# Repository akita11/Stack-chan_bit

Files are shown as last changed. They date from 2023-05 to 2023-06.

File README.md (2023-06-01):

# Stack-chan_bit

[ｽﾀｯｸﾁｬﾝ](https://protopedia.net/prototype/2345Stack-chan)に[micro:bit](https://www.switch-science.com/products/7952)を差し込んで制御するボードです。micro:bitのプログラミングでｽﾀｯｸﾁｬﾝを動かすことができます。

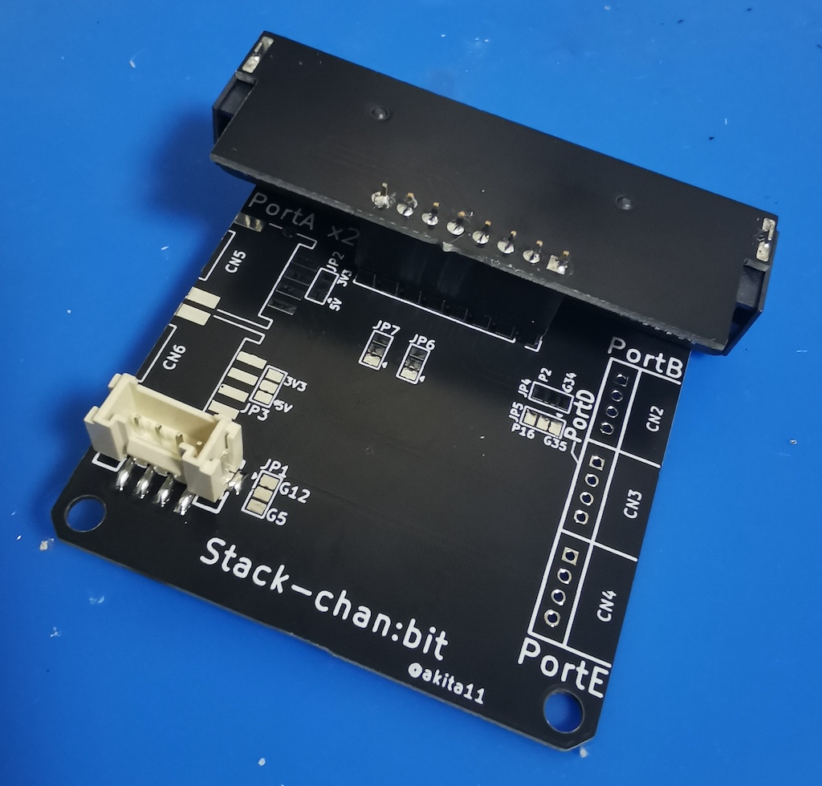
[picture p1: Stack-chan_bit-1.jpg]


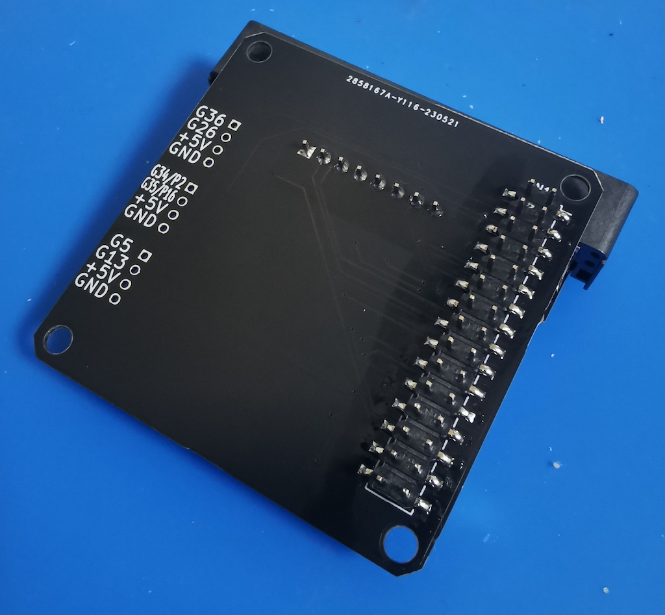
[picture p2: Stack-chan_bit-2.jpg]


## 使用例

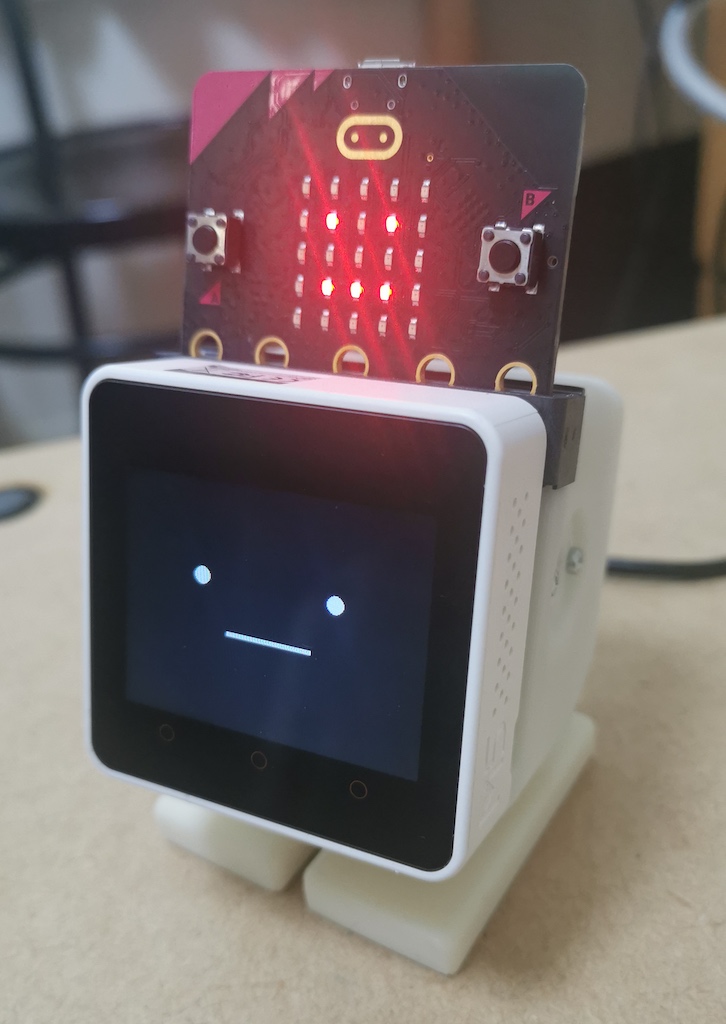
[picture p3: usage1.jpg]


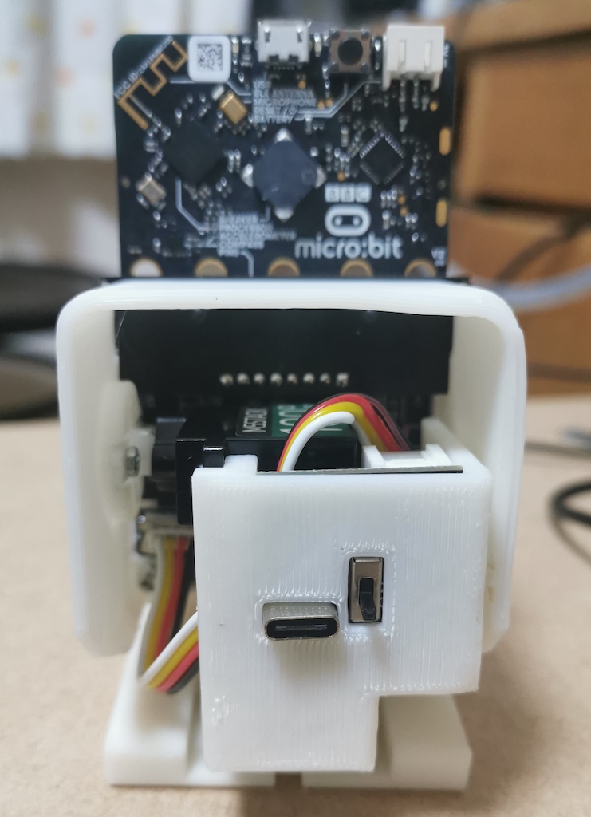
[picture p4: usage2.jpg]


micro:bit側のプログラム（m-asaoka-fap氏作成の[カスタムブロック](https://github.com/m-asaoka-fap/stackchanbit_2)あり）から、ｽﾀｯｸﾁｬﾝを制御できます。→[使用例](https://twitter.com/akita11/status/1656496746321842176)

## 作り方

### 用意するもの

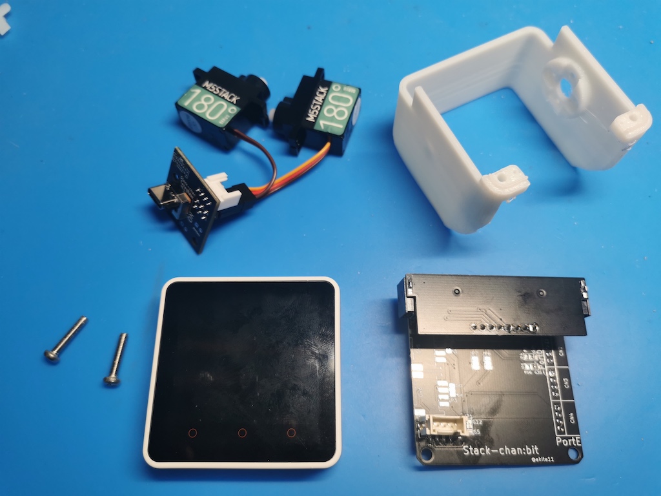
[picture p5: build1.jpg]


- M5Stack (BasicまたはCore2がオススメ)
- [Stack-chan_Takao_Base](https://github.com/akita11/Stack-chan_Takao_Base)とそれで用いるもの（サーボモータ2個、Groveケーブル、ネジ等、筐体(shell部以外)）※顔部分のM5Stack本体との固定には、BasicではM3x15mm、Core2ではM3x20mmのネジを2本使います
- shell部の筐体(Stack-chan_bit_shell.stlを3Dプリントしたもの): [タカオ版筐体](https://github.com/meganetaaan/stack-chan/tree/dev/v1.0/case/contributed/mongonta_case_for_SG90_and_M5GoBottomBoard/case_for_SG90andM5GoBottomBoard)内の”shell_SG90_basicgraybottom_v1.0.stl"を元に改変

### 組み立て

M5Stackに専用プログラム（FW_PIO/以下。PlatformIO用）を書き込みます。

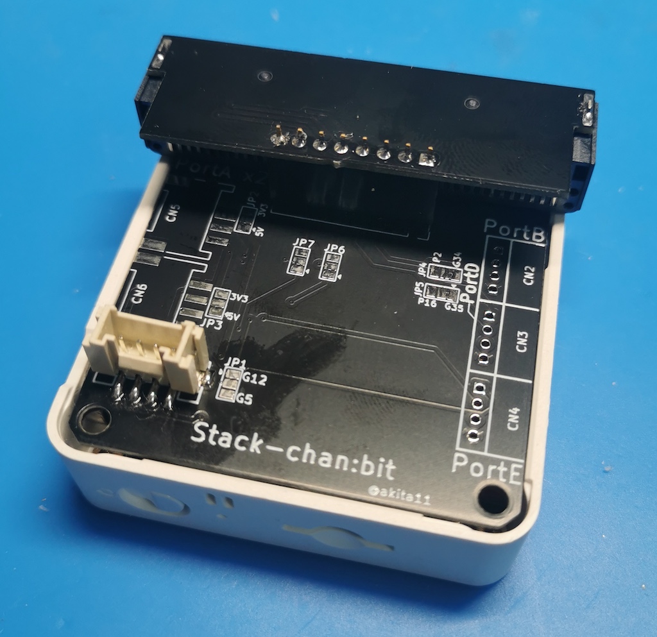
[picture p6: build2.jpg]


M5Stackの底板を外し、Stack-chan_bitをさしこみます。

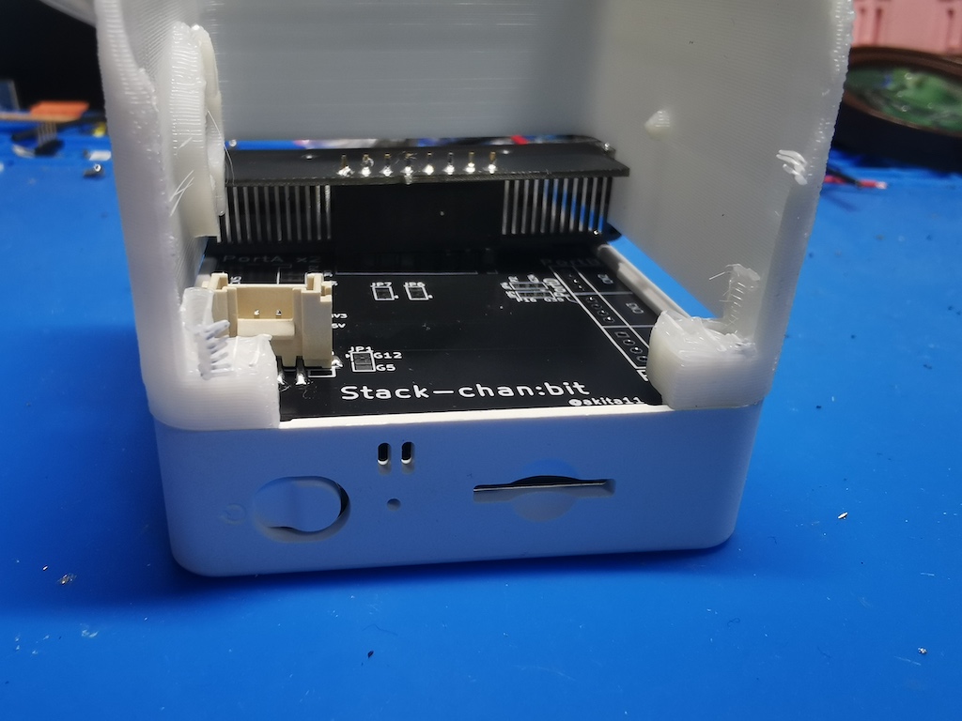
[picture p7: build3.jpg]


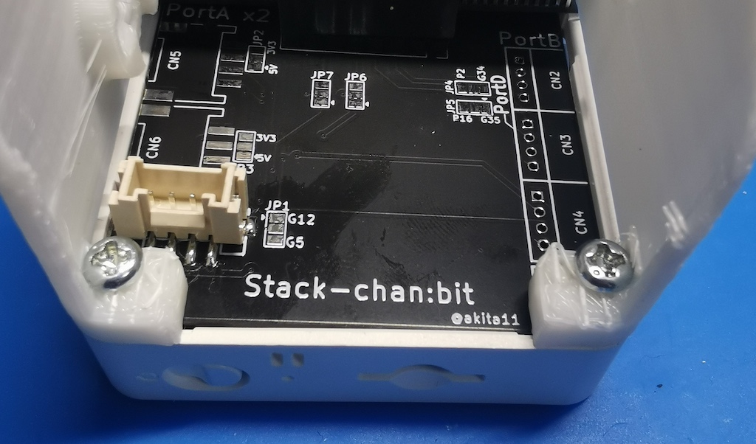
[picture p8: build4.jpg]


2本のM3ネジで固定します

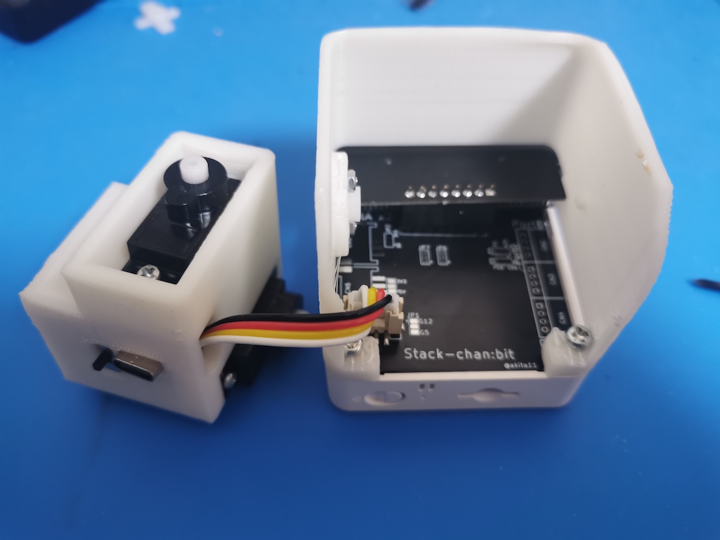
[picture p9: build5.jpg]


[Stack-chan_Takao_Base](https://github.com/akita11/Stack-chan_Takao_Base)を使って
Bracket部（サーボ2個が固定される部分）を組み立てつつ、Stack-chan:bit基板と、Groveケーブルで接続します。

残りの部分は、Stack-chan_Takao_BaseからのGroveケーブルは、M5Stack本体ではなく、Stack-chan_bitのGroveコネクタに接続する

残りの部分は、[タカオさんの手順](https://raspberrypi.mongonta.com/how-to-build-easy-stackchan-m5gobottom/)を参考に組み立てます。

## プログラミング

micro:bitとｽﾀｯｸﾁｬﾝ(M5Stack)の間はUART通信(115200bps・N81、コマンド区切りはLF/0x0a/'\n'）で以下のような制御コマンドを送って制御します。[micro:bit側のカスタムブロック](https://github.com/m-asaoka-fap/stackchanbit_2)もあり、MakeCoreで組み込んで使用できます。

- 動作の制御
  - Xnn : パン動作（横方向）nn=角度、範囲＝-90〜90（正面=0）
  - Ynn : チルト動作（縦方向）nn=角度、範囲=0〜30（正面=0から上向きへ）
- 顔の制御
  - Txxxx : 吹き出しに”xxxx”と表示し、それにあわせて口が動く
  - En : 表情を設定。n=0〜5 (0=Angry, 1=Sleepy, 2=Happy, 3=Sat, 4=Doubt, 5=Neutral)

## （おまけ）拡張用Grove端子

M5Stackやmicro:bitの一部の端子をGrove端子に引き出せるようにGroveコネクタ実装部が用意してあります。詳細は回路図を参照してください。ただし使用する場合はGroveコネクタ部分にあわせて筐体(shell)の修正が必要になります。

## Author

Junichi Akita (@akita11, akita@ifdl.jp)

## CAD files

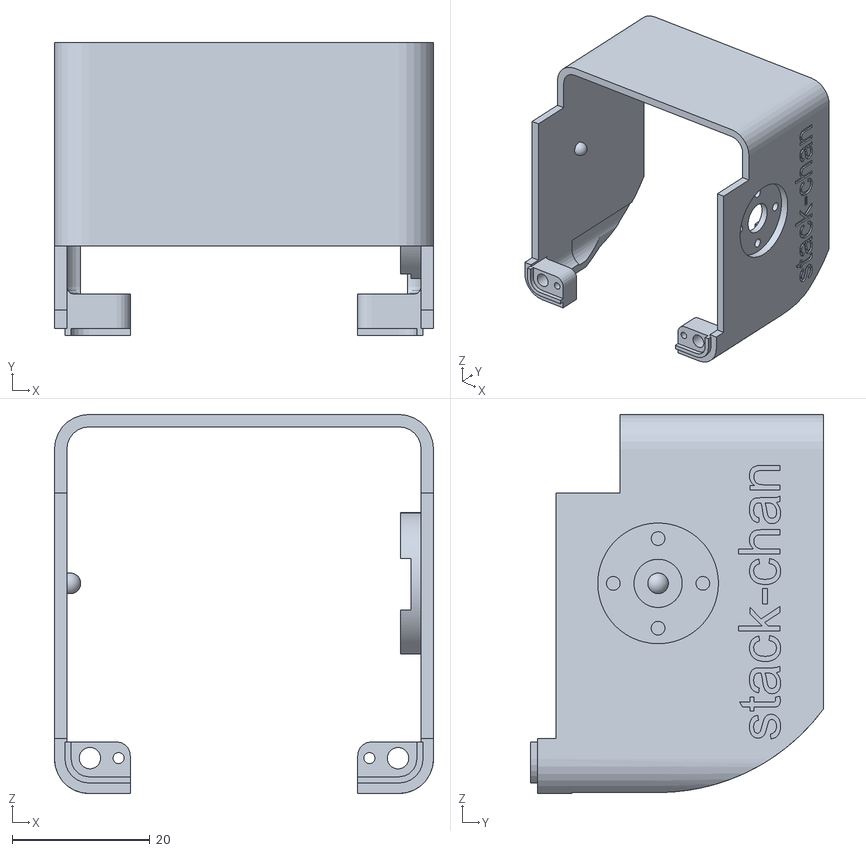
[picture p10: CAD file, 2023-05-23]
Stack-chan_bit_shell.stl
55.0 x 42.5 x 55.0

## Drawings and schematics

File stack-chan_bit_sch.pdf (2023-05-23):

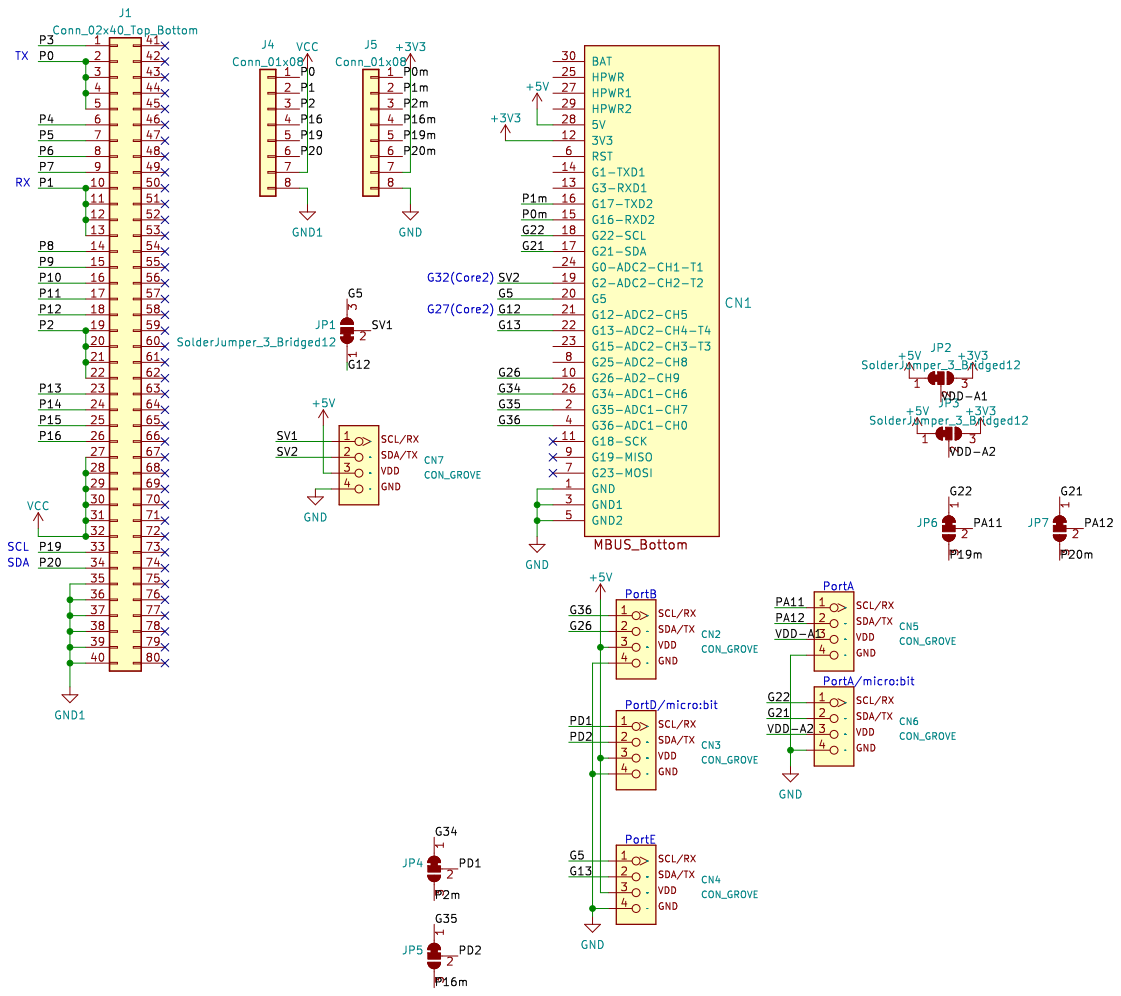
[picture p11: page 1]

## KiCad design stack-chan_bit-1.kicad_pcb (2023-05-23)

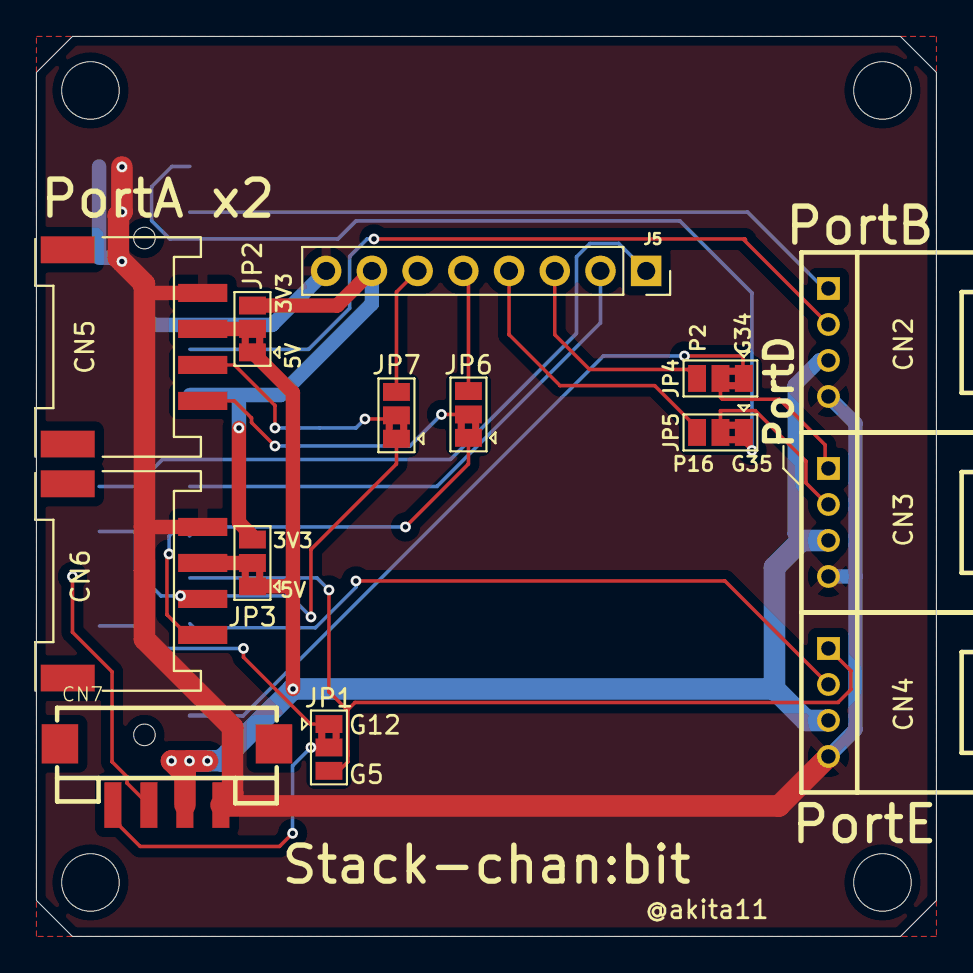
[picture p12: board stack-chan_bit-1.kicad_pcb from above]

Board: 2 copper layers, 50.0 x 50.0 mm, 15 parts (1 on the bottom side), 26 nets.

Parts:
CN1: CON_MBUS_bottom; PinSocket_2x15_P2.54mm_Vertical_SMD
CN2, CN3, CN4: CON_GROVE; CON_GROVE_H
CN5, CN6: CON_GROVE; CON_GROVE_H_SMD
CN7: CON_GROVE; CON_GROVE_V_SMD
J5: Conn_01x08; PinSocket_1x08_P2.54mm_Vertical
JP1, JP2, JP3, JP4, JP5, JP6, JP7: SolderJumper_3_Bridged12; SolderJumper-3_P1.3mm_Bridged2Bar12_Pad1.0x1.5mm

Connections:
+3V3: CN1.12 (3V3), J5.7, JP2.3 (B), JP3.3 (B)
+5V: CN1.28 (5V), CN2.3, CN3.3, CN4.3, CN7.3, JP2.1 (A), JP3.1 (A)
/G5: CN1.20 (G5), CN4.1, JP1.3 (B)
/G12: CN1.21 (G12-ADC2-CH5), JP1.1 (A)
/G13: CN1.22 (G13-ADC2-CH4-T4), CN4.2
/G21: CN1.17 (G21-SDA), CN6.2, JP7.1 (A)
/G22: CN1.18 (G22-SCL), CN6.1, JP6.1 (A)
/G26: CN1.10 (G26-AD2-CH9), CN2.2
/G34: CN1.26 (G34-ADC1-CH6), JP4.1 (A)
/G35: CN1.2 (G35-ADC1-CH7), JP5.1 (A)
/G36: CN1.4 (G36-ADC1-CH0), CN2.1
/P0m: CN1.15 (G16-RXD2), J5.1
/P1m: CN1.16 (G17-TXD2), J5.2
/P2m: J5.3, JP4.3 (B)
/P16m: J5.4, JP5.3 (B)
/P19m: J5.5, JP6.3 (B)
/P20m: J5.6, JP7.3 (B)
/PA11: CN5.1, JP6.2 (C)
/PA12: CN5.2, JP7.2 (C)
/PD1: CN3.1, JP4.2 (C)
/PD2: CN3.2, JP5.2 (C)
/SV1: CN7.1, JP1.2 (C)
/SV2: CN1.19 (G2-ADC2-CH2-T2), CN7.2
/VDD-A1: CN5.3, JP2.2 (C)
/VDD-A2: CN6.3, JP3.2 (C)
GND: CN1.1 (GND), CN1.3 (GND1), CN1.5 (GND2), CN2.4, CN3.4, CN4.4, CN5.4, CN6.4, CN7.4, J5.8

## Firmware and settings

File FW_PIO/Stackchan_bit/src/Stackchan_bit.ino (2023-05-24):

#include <Arduino.h>

#include <M5Unified.h>
#if defined(ARDUINO_M5STACK_Core2)
  #define SERVO_PIN_X 27
  #define SERVO_PIN_Y 32
  #define UART_PIN_TXD 14
  #define UART_PIN_RXD 13
#elif defined(ARDUINO_M5Stack_Core_ESP32)
  #define SERVO_PIN_X 12
  #define SERVO_PIN_Y 2
  #define UART_PIN_TXD 17
  #define UART_PIN_RXD 16
#endif

#define X_MIN -90  // [deg]
#define X_MAX 90   // [deg]
#define Y_MIN 0    // [deg]
#define Y_MAX 30   // [deg]
#define E_MIN 0    // emotion num
#define E_MAX 6    // emotion num

int servo_offset_x = 0;  // X軸サーボのオフセット（90°からの+-で設定）
int servo_offset_y = 0;  // Y軸サーボのオフセット（90°からの+-で設定）

#include <Avatar.h> // https://github.com/meganetaaan/m5stack-avatar
#include <ServoEasing.hpp> // https://github.com/ArminJo/ServoEasing       
#include "formatString.hpp" // https://gist.github.com/GOB52/e158b689273569357b04736b78f050d6

#define RX_BUF_SIZE 32
char RXbuf[RX_BUF_SIZE];
uint8_t pRX = 0;

using namespace m5avatar;
Avatar avatar;

const Expression expressions[] = {
  Expression::Angry,
  Expression::Sleepy,
  Expression::Happy,
  Expression::Sad,
  Expression::Doubt,
  Expression::Neutral
};

#define START_DEGREE_VALUE_X 90
#define START_DEGREE_VALUE_Y 90

ServoEasing servo_x;
ServoEasing servo_y;

uint32_t mouth_wait = 2000;  // 通常時のセリフ入れ替え時間（msec）
uint32_t last_mouth_millis = 0;

const char* lyrics[] = { "BtnA:MoveTo90  ", "BtnB:ServoTest  ", "BtnC:RandomMode  ", "BtnALong:AdjustMode" };
const int lyrics_size = sizeof(lyrics) / sizeof(char*);
int lyrics_idx = 0;

void moveX(int x, uint32_t millis_for_move = 0) {
  if (millis_for_move == 0) {
    servo_x.easeTo(x + servo_offset_x);
  } else {
    servo_x.easeToD(x + servo_offset_x, millis_for_move);
  }
}

void moveY(int y, uint32_t millis_for_move = 0) {
  if (millis_for_move == 0) {
    servo_y.easeTo(y + servo_offset_y);
  } else {
    servo_y.easeToD(y + servo_offset_y, millis_for_move);
  }
}

void moveXY(int x, int y, uint32_t millis_for_move = 0) {
  if (millis_for_move == 0) {
    servo_x.setEaseTo(x + servo_offset_x);
    servo_y.setEaseTo(y + servo_offset_y);
  } else {
    servo_x.setEaseToD(x + servo_offset_x, millis_for_move);
    servo_y.setEaseToD(y + servo_offset_y, millis_for_move);
  }
  // サーボが停止するまでウェイトします。
  synchronizeAllServosStartAndWaitForAllServosToStop();
}

void adjustOffset() {
  // サーボのオフセットを調整するモード
  servo_offset_x = 0;
  servo_offset_y = 0;
  moveXY(90, 90);
  bool adjustX = true;
  for (;;) {
    M5.update();
    if (M5.BtnA.wasPressed()) {
      // オフセットを減らす
      if (adjustX) {
        servo_offset_x--;
      } else {
        servo_offset_y--;
      }
    }
    if (M5.BtnB.pressedFor(2000)) {
      // 調整モードを終了
      break;
    }
    if (M5.BtnB.wasPressed()) {
      // 調整モードのXとYを切り替え
      adjustX = !adjustX;
    }
    if (M5.BtnC.wasPressed()) {
      // オフセットを増やす
      if (adjustX) {
        servo_offset_x++;
      } else {
        servo_offset_y++;
      }
    }
    moveXY(90, 90);

    std::string s;

    if (adjustX) {
      s = formatString("%s:%d:BtnB:X/Y", "X", servo_offset_x);
    } else {
      s = formatString("%s:%d:BtnB:X/Y", "Y", servo_offset_y);
    }
    avatar.setSpeechText(s.c_str());
  }
}

void moveRandom() {
  for (;;) {
    // ランダムモード
    int x = random(45, 135);  // 45〜135° でランダム
    int y = random(60, 90);   // 50〜90° でランダム
    M5.update();
    if (M5.BtnC.wasPressed()) {
      break;
    }
    int delay_time = random(10);
    moveXY(x, y, 1000 + 100 * delay_time);
    delay(2000 + 500 * delay_time);
    //avatar.setSpeechText("Stop BtnC");
    avatar.setSpeechText("");
  }
}

int getParam()
{
  return(atoi(RXbuf+1));
}

void setup() {
  auto cfg = M5.config();
  M5.begin(cfg);
  Serial2.begin(115200, SERIAL_8N1, UART_PIN_RXD, UART_PIN_TXD);
  while (!Serial2)
    ;

  if (servo_x.attach(SERVO_PIN_X,
                     START_DEGREE_VALUE_X + servo_offset_x,
                     DEFAULT_MICROSECONDS_FOR_0_DEGREE,
                     DEFAULT_MICROSECONDS_FOR_180_DEGREE)) {
    Serial.print("Error attaching servo x");
  }
  if (servo_y.attach(SERVO_PIN_Y,
                     START_DEGREE_VALUE_Y + servo_offset_y,
                     DEFAULT_MICROSECONDS_FOR_0_DEGREE,
                     DEFAULT_MICROSECONDS_FOR_180_DEGREE)) {
    Serial.print("Error attaching servo y");
  }
  servo_x.setEasingType(EASE_QUADRATIC_IN_OUT);
  servo_y.setEasingType(EASE_QUADRATIC_IN_OUT);
  setSpeedForAllServos(60);
  avatar.init();
  last_mouth_millis = millis();
  //moveRandom();
}

void loop() {
  M5.update();
  if (M5.BtnA.pressedFor(2000)) {
    // サーボのオフセットを調整するモードへ
    adjustOffset();
  }
  if (M5.BtnA.wasPressed()) {
    Serial2.println("A");
    moveXY(90, 90);
  }

  if (M5.BtnB.wasPressed()) {
    Serial2.println("B");
    for (int i = 0; i < 2; i++) {
      avatar.setSpeechText("X 90 -> 0  ");
      moveX(0);
      avatar.setSpeechText("X 0 -> 180  ");
      moveX(180);
      avatar.setSpeechText("X 180 -> 90  ");
      moveX(90);
      avatar.setSpeechText("Y 90 -> 50  ");
      moveY(50);
      avatar.setSpeechText("Y 50 -> 90  ");
      moveY(90);
    }
  }
  if (M5.BtnC.wasPressed()) {
    // ランダムモードへ
    moveRandom();
  }
/*
  if ((millis() - last_mouth_millis) > mouth_wait) {
    const char* l = lyrics[lyrics_idx++ % lyrics_size];
    avatar.setSpeechText(l);
    avatar.setMouthOpenRatio(0.7);
    delay(200);
    avatar.setMouthOpenRatio(0.0);
    last_mouth_millis = millis();
  }
  */
  if (Serial2.available()) {
    char c = Serial2.read();
    RXbuf[pRX++] = c;
    if (c == '\n' || pRX >= RX_BUF_SIZE - 1) {
      RXbuf[pRX] = '\0';
      pRX = 0;
      Serial.println(RXbuf);
      int param;
      switch (RXbuf[0]) {
        case 'X':
          param = getParam();
          if (param < X_MIN) param = X_MIN;
          if (param > X_MAX) param = X_MAX;
//	        Serial.println(param);
          moveX(param + START_DEGREE_VALUE_X);
          break;
        case 'Y':
          param = getParam();
          if (param < Y_MIN) param = Y_MIN;
          if (param > Y_MAX) param = Y_MAX;
//	        Serial.println(param);
          moveY(-param + START_DEGREE_VALUE_Y);
          break;
        case 'T':
          avatar.setSpeechText(RXbuf + 1);
	  for (int i = 0; i < 3; i++){
            avatar.setMouthOpenRatio(0.7);
            delay(200);			
            avatar.setMouthOpenRatio(0);
            delay(200);			
	  }
          break;
        case 'E':
          param = getParam();
          if (param < E_MIN) param = E_MIN;
          if (param > E_MAX) param = E_MAX;
          avatar.setExpression(expressions[param]);
          break;
      }
    }
  }
}

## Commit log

2023-05-23 update shell stl
    [Stack-chan_bit_shell.stl]
2023-05-24 fix pin assignment for Core2
    [Stackchan_bit.ino]
2023-06-01 add README, optional Grove connector
